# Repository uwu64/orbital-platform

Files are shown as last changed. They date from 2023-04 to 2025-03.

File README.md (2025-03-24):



# Orbital Platform

Integrated flight systems board with flight controller, avionics & instrumentation, radio, science, and development support for UC Davis Space and Satellite Systems REALOP-1 mission.

It's nearly all you need to fly a simple satellite and perform interesting experiments and observations 

## Documentation:

For an overview of the project, some FAQs, and links to some other documentation, see the [Cattleworks Compendium](https://docs.google.com/document/d/1Hi_DiSkjC-WS4wI39fk3itqsipQI5O-aAOiK9zkmOj8/edit#)

Pinout and usage information of Revision 3 can be found in the [OPR3 Reference Manual](https://docs.google.com/document/d/1Jm04JslQRQYXkw6q29EbMsp4aHQEIRqEN40WjQPSD0c/edit?usp=sharing)

Other useful documents include
- [STM32L47xxx reference manual](https://www.st.com/resource/en/reference_manual/rm0351-stm32l47xxx-stm32l48xxx-stm32l49xxx-and-stm32l4axxx-advanced-armbased-32bit-mcus-stmicroelectronics.pdf)
- [STM32L476xx datasheet](https://www.st.com/resource/en/datasheet/stm32l476zg.pdf)

Find IntelliSat developed by the flight software team at [the IntelliSat repository](https://github.com/Space-and-Satellite-Systems-UC-Davis/IntelliSat), including [detailed documentation about widgets and connections](https://github.com/Space-and-Satellite-Systems-UC-Davis/IntelliSat/blob/main/Manuals/OrbitalPlatform_Hardware/OP_Hardware.md). 

### Toolchain
Besides Flight Software's IntelliSat, I recommend that you try my [minimum development template](https://github.com/uwu64/cg3-stm32l476) that includes the exact bare minimum to compile and deploy firmware to Orbital Platform. The only dependencies are GCC for arm, pyocd, and make. 



## Revision 3

Revision 3 is in the validation stage, with many changes and additions. 

Some themes and guidelines for Revision 3: 
- Keep software compatibility with R2. Remap a minimal number of pins and don't change existing peripherals. 
- Further improve manufacturability.
- Include radio system (Orbital Imager will be deprecated)
  - Relatedly, we need a new camera interface port. Likely UART or SPI
- Possibly introduce additional features 
  - More connectors: Coils, panel temperature sensors, etc. 
  - More sensors: High precision temperature sensor, and digitizer for additional thermistors or sensors 
- Mechanical adjustments to meet any changes to structures, and possible compatibility with High Altitude Balloon project 
- Direct battery voltage measurement 
- Current sensor and power switches for ADCS science and experiment payloads
- Another redundant set of avionics (IMU and mag) for good vibes. IMU does not need to be at dead center of board anymore
- Multiple connectors and associated pins for features like HDD-ESC and sun sensors
- Heart beat LED on PE2 

Errata: a few things need to be fixed 
- Re-pour copper planes to fix two shorted vias
- Correct the direction of the PMOS high side switch for the pyro/antenna deployment heater
- MCU ADC Vref needs to be tied to either 3.3 V or external reference 

Related electrical team design tasks: 
- Three channel constant current driver for magnetorquer
- Hard disk drive motor driver

Inter-board connector list for Rev 3
| Mnemonic | Multiplicity | Connector type | Purpose |
| --- | --- | --- | --- |
| esc | 1 | Picoblade 4 pin | HDD driver speed command and feedback |
| coil | 1 (3 axis) | Picoblade 4 pin | Magnetorquer driver control signal and I V feedback |
| sol | 4-6 | Picoblade 8 pin | Sun sensor photodiodes and outer panel thermistors |
| mbat | 1 | Picoblade 8 pin | Satellite main battery |
| cam | 1 | Picoblade 8 pin | Imaging system data connection | 
| pyro | 1 | Picoblade 4 pin | Antenna melt-wire deployer |
| pv | 4 | Picoblade 8 pin | Photovoltaic cell (solar panel) power input from each panel |
| inst | 1-2 | Picoblade 8 pin | Auxiliary instrumentation bus (I2C) for remote ADCs |
| service | 1 | JST GH | Ground diagnostic and firmware service port (SWD, UART) | 
| topoff | 1 | N/A | Ground battery top-off charging port |
| rbf | 1 | N/A | Remove before flight safety interlock |
| aux | 1-4 | Picoblade 8 pin | Auxillary UART/I2C/SPI ports | 
| usb | 1 | USB Type-C | Ground use USB port |
| trx | 1 | MMCX | Antenna coaxial RF connection to radio system |

(Service and Topoff ports could be combined into "umbilical" port?)

Featured chips: (Many ~~chips~~ are removed for Revision 2. See below.)
 - STM32L476ZGT3 (microcontroller)
 - ASM330LHH (inertial sensor)
 - QMC5883L (magnetometer)
 - ~~ADF7021 (radio front end)~~ 
 - ~~TQP7M9102 (power amplifier)~~ 
 - ~~SKY13453 (rf switch)~~
 - ~~MAX2208 (rf power detector)~~ 
 - W25Q128JVSIQ (flash memory) 
 - MB85RS256B (ferroelectric memory)
 - ~~TMP235 (analog temperature sensor)~~ 

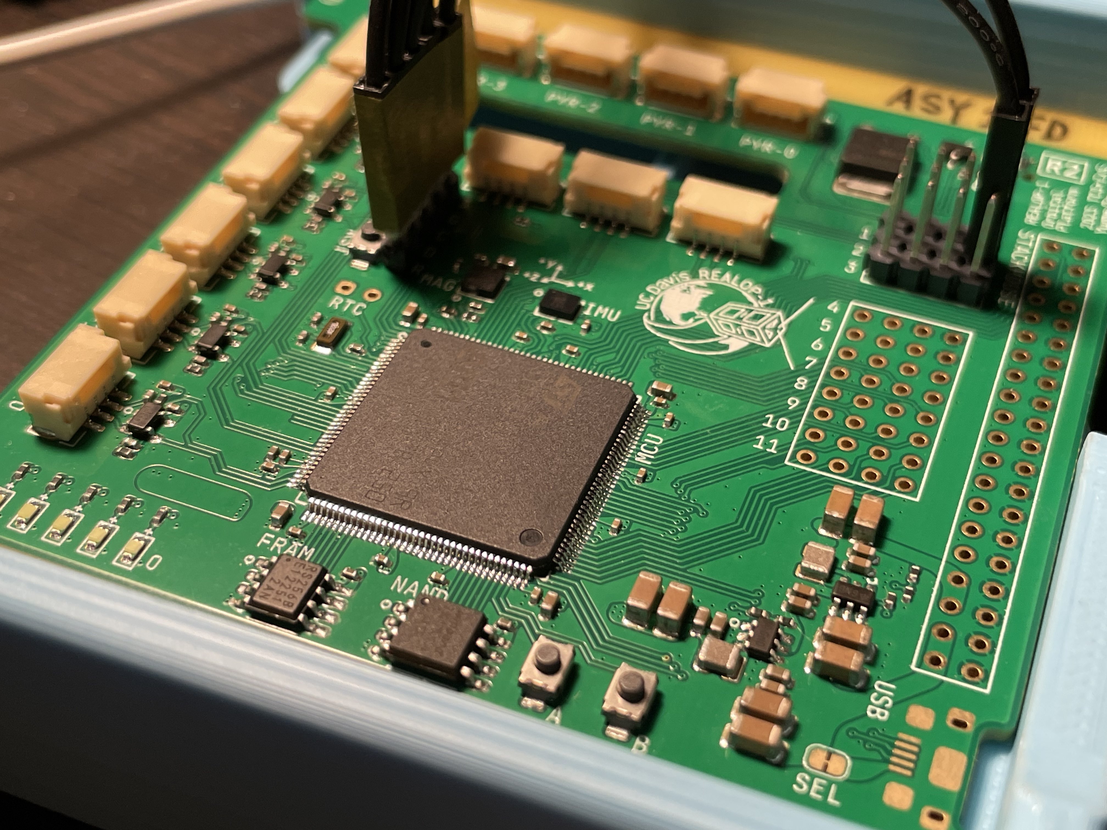
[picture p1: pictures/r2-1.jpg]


## Revision 2

Revision 2 hardware of Orbital Platform is in the verification stage. So far, so good!

### Changes 
- Removed radio system: communication function delegated to the new [Orbital Imager](https://github.com/REALOP-ELEC/Orbital_Imager_LRes) 
- Revised layout to improve routing, manufactuability, and reliabiltiy
- Inertial sensor (ASM330LHH) is now connected via SPI for reliability
- Magnetometer (QMC5883L) on its own I2C bus for reliability
- Addition of JST-GH connectors for
  - 6x Solar panels (photodiode + thermistor)
  - 4x Solar panels (pyramid design) 
  - ESC control via PWM
  - ESC control via UART
  - Expansion UART
- Addition of pyrotechnic channel to drive antenna deployment meltwire
- Less LEDs (still a usable amount)
- Fixed EXTI pins: no overlapping signals
- Fixed USB FS implementation 
- Design for manufacturability: reduced cost and BOM lines

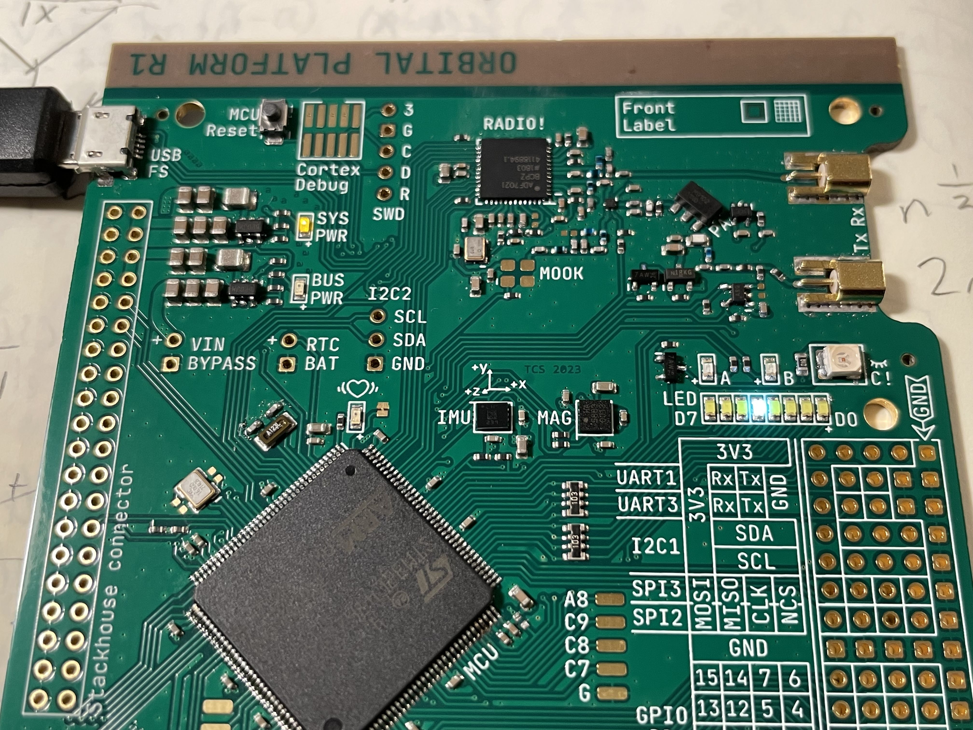
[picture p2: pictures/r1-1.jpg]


## Revision 1

Revision 1 was the initial prototype that we used to validate whether our choice of components are suited for the application. 

# Getting started

Orbital Platform should be delivered to you with a test program flashed, where it blinks the indicator LEDs in a demo pattern. 

To program and debug the MCU, attach a SWD-compatible debugger like ST-LINK, JLINK, or DAPLINK, to the SWD connector near the MCU. 
| Label | Signal |
| --- | --- |
| 3 | 3.3 V  |
| G | Ground |
| C | SWCLK  |
| D | SWDIO  |
| R | NRST |

The reset button is next to the SWD header, labelled RST. 

Use your toolchain of choice to target the `stm32l476zgt` MCU. 

## Using the gcc-arm-none-eabi toolchain and pyocd with DAPLINK debugger
I personally prefer to use a very minimal environment for prototyping firmware. See the [template project here](https://github.com/uwu64/cg3-stm32l476)

## Using the Keil MDK (μVision) IDE with DAPLINK debugger

One toolchain that works with developing software for Orbital Platform uses the Keil MDK IDE and DAPLINK debugger dongle, on Windows. 
- Start by downloading and installing a free version of Keil MDK-ARM (μVision). You should be able to download it after filling out some info on [the download page](https://www.keil.com/demo/eval/arm.htm)
  - The free version now seems to be called "MDK-Community" and appears to be a non-commercial but fully featured version of the normal IDE. It used to be that the demo/eval/free version had a very restricted code size. Hope this is no longer the case.
- Also download and install STM32CubeMX which is ST's initialization code generator and graphical config editor. Scroll down on [this page](https://www.st.com/en/development-tools/stm32cubemx.html) to Get Software. You might need to fill in some info for this as well. 
- Launch the IDE.
- Find the "Pack Installer" in the top toolbar. It looks like a green diamond shape with four dots inside.
- Use the Pack Installer to install relevant CMSIS device support packs for `STM32L4 Series`
- Close Pack Installer. From the top toolbar, use the menu `Project` -> `New μVision Project` to start a new project.
- When given the option to select target device, choose `STM32L476ZGTx`
- When given the option to manage run time environment, enable `CMSIS -> CORE`, `Device -> Startup`, `Device -> STM32Cube HAL`. There may be dependancies highlighted in yellow, enable those too.
  - Also enable `Device -> STM32Cube Framework (API) -> STM32CubeMX`. If it requires you to press the button to launch CubeMX, do it. Try to proceed with default settings in CubeMX because we don't intend to use any generated code.
  - Don't enable anything else unless you want to use full HAL or other middleware.
- After creating a new project, open `Options for Target` in the top toolbar. Then go to the `Debug` tab and choose Use `CMSIS-DAP debugger`. No additional configuration should be needed.
  - Or choose whatever debugger you use, like ST-Link or J-Link.
- In the left side `Project` panel, right click `Source Group 1` and select `Add new Item to Group`
  - Choose `C File (.c)` and name it `main.c`
  - You need to `#include <stm32l476xx.h>` to import register definitions.
  - Paste some code from this repository or write some blinky program.
  - Alternatively, you can git clone or zip download this repository and directly open the Keil project files. Everything should be configured for DAPLINK targeting Orbital Platform.
- Connect Orbital Platform to DAPLINK via the SWD port. Plug DAPLINK to your computer.
  - The DAPLINK should light up, if it doesn't, unplug it from your computer immediately and check your wiring. There may be a short circuit.
- Click `Build` on the top toolbar, then `Download`. Your code should now be compiled and flashed to Orbital Platform. Click `Debug` to launch the debugger, or signal a hardware reset to begin execution.

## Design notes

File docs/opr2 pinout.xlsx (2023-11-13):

Orbital Platform R2 |  | Pin definitions | Tim S. 2023 10 25 19 16
Pin | AF/Mode | Signal name | Definition
Pyro channel (melt-wire connector on bottom side)
PA0 | GPIO OUT | pyro-gate | High side switch control signal. Active high.
PA3 | ADC IN | pyro-isen | Current monitor for melt-wire. Voltage is proportional to current.
Solar panel sensor connectors (SOL-x)
PA1 | ADC IN | ntc-0 | Thermister divider output.
PA2 | ADC IN | pd-0 | Photodiode transimpedance amplifier output.
PC2 | ADC IN | ntc-1 | As above
PC3 | ADC IN | pd-1 | As above
PF9 | ADC IN | ntc-2 | As above
PF10 | ADC IN | pd-2 | As above
PF7 | ADC IN | ntc-3 | As above
PF8 | ADC IN | pd-3 | As above
PF5 | ADC IN | ntc-4 | As above
PF6 | ADC IN | pd-4 | As above
PF4 | ADC IN | ntc-5 | As above
PF3 | ADC IN | pd-5 | As above
Sun sensor pyramid connectors (PYR-x)
PF0 | AF I2C | sun-sda | I2C bus for sun sensor pyramids
PF1 | AF I2C | sun-scl | I2C bus for sun sensor pyramids
ESC controller (ESC-x)
PA15 | AF TMR CHx | esc-pwm | PWM output for ESC
PB6 | AF UART | esc-uart-tx | UART for custom ESC
PB7 | AF UART | esc-uart-rx | As above
Science expansion port (SCI-A)
PC0 | AF UART | sci-uart-rx | UART for future use
PC1 | AF UART | sci-uart-tx | As above
IMU on SPI3
PB3 | AF SPI | imu-sck
PB4 | AF SPI | imu-miso
PB5 | AF SPI | imu-mosi
PG15 | GPIO OUT | imu-ncs
PG12 | GPIO IN PU | imu-int1
PG13 | GPIO IN PU | imu-int2
MAG on I2C1
PB8 | AF I2C | mag-scl
PB9 | AF I2C | mag-sda
PE0 | EXTI0 | mag-drdy
FRAM on SPI1
PA4 |  | fram-ncs
PA5 |  | fram-sck
PA6 |  | fram-miso
PA7 |  | fram-mosi
PC4 |  | fram-nwp
PC5 |  | fram-nhold
NAND on QSPI
PE10 |  | nand-sck
PE11 |  | nand-ncs
PE12 |  | nand-d0
PE13 |  | nand-d1
PE14 |  | nand-d2
PE15 |  | nand-d3
Stackhouse power regulator
PB12 | GPIO OUT | vout-en | Enable signal for regulator
PB13 |  | vout-pg | Power good signal from regulator. Active low when voltage is in range
Indicator LEDs
PE2 | GPIO OUT | led4
PE3 | GPIO OUT | led3
PE4 | GPIO OUT | led2
PE5 | GPIO OUT | led1
PE6 | GPIO OUT | led0
User buttons
PB10 | GPIO IN PU | btn-a
PB11 | GPIO IN PU | btn-b
Stackhouse connector
PD15 |  | stack-bus-good
PG2 |  | stack-pa-en
PG3 |  | stack-pa-temp
PG4 |  | stack-pa-det
PG5 |  | stack-rfd-temp
PG8 |  | stack-i2c-sda
PG7 |  | stack-i2c-scl
PC10 |  | instbus-int0
PC11 |  | radiobus-int0
PD0 |  | radio-spi-cs
PD3 |  | radio-spi-rofi
PD4 |  | radio-spi-rifo
PD1 |  | radio-spi-clk
Debug GPIOs (labeled from left to right, 1 to 4)
1-1 | GND
1-2 | esc-pwm
1-3 | esc-uart-rx
1-4 | esc-uart-tx
2-1 | mag-scl
2-2 | imu-mosi
2-3 | imu-ncs
2-4 | sci-uart-rx
3-1 | mag-sda
3-2 | imu-miso
3-3 | imu-sck
3-4 | sci-uart-tx
4-1 | 3V3
4-2 | 3V3
4-3 | GND
4-4 | GND
5-1 | PF15
5-2 | PF14
5-3 | PF13
5-4 | GND
6-1
6-2
6-3
6-4

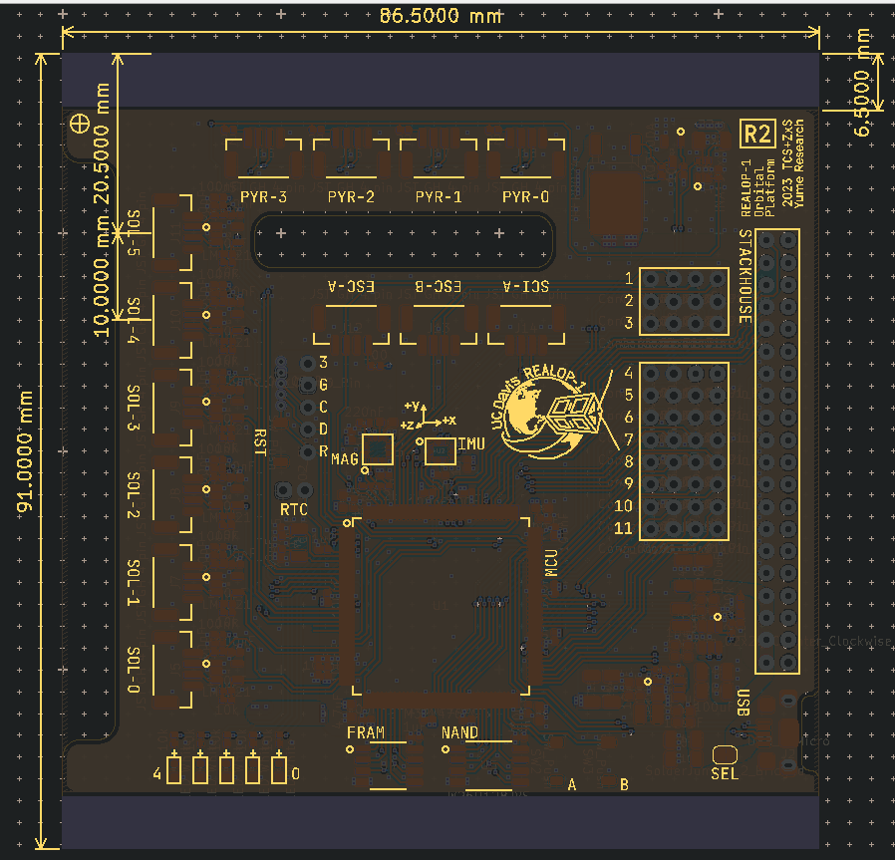
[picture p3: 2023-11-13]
docs/r2-mech.png

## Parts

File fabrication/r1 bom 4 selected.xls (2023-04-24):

Comment | Designator | Footprint | JLCPCB Part #
1n | C48,C50,C59,C70,C73 | C0402 | C113780
3.3k | R32 | C0402 | C25890
1.5k | R6 | C0402 | C25867
22u | C1,C2,C3,C4,C5,C42,C43,C44,C45,C46 | C0805 | C45783
LEDRed | D11 | LED0603v2 | C84263
220 | R42 | C0402 | C25117
4.7k | R7,R8,R13,R14,R15,R16,R26,R28,R33,R34 | C0402 | C25900
10k | R9,R10,R11,R12,R17,R20,R21,R22,R25,R36,R37,R38,R39 | C0402 | C25744
32.768k | X1 | XO3215-2P | C32346
24M | X2 | XO3225 | C13738
100k | R1,R18 | C0402 | C25741
LEDWhite | D1,D2,D3,D4,D5,D6,D7,D8 | LED0603v2 | C84265
LEDBlue | D12,D15 | LED0603v2 | C84266
10 | R24 | C0402 | C25077
10p | C52 | C0402 | C32949
2.7p | C74,C75 | C0402 | C1561
3.3p | C56,C71,C72 | C0402 | C1565
10u | C26,C60,C61,C62,C63,C64,C65,C68,C69,C76 | C0603 | C19702
22p | C47,C51 | C0402 | C1555
1u | C6,C12,C13,C14,C15,C16,C17,C18,C23,C24,C25,C27,C29,C30,C31,C32,C33,C34,C35,C36,C37,C38,C39,C40,C41,C49,C53,C55,C58,C66,C77,C80 | C0402 | C52923
220n | C67 | C0402 | C16772
100p | C79,C81 | C0402 | C1546
15p | C78 | C0402 | C1548
10k | R4,R5 | R0603x4 | C29718
1k | R3,R29,R30,R31,R44 | C0402 | C11702
6.8n | C20 | C0402 | C1542
FB0603 | FB1 | C0603 | C13415
LEDYellow | D9,D13,D14 | LED0603v2 | C72038
100n | C19,C21,C28,C54,C57 | C0402 | C1525
22n | C22 | C0402 | C1532
2.2n | C9 | C0402 | C1531
100 | R35 | C0603 | C22775
LEDGreen | D10 | LED0603v2 | C84267
0 | R40,R41 | C0402 | C17168
39n | L7,L8 | C0402 | C269823
ICQMC5883L | U9 | LGA16-5 | C976032
56n | L6,L9,L10 | C0402 | C167484
22k | R2,R19 | C0402 | C25768
QSi2301 | Q2 | SOT23-3 | C10487
ICSKY13453 | U8 | QFN6 | C150878
10n | L5,L12 | C0402 | C90642

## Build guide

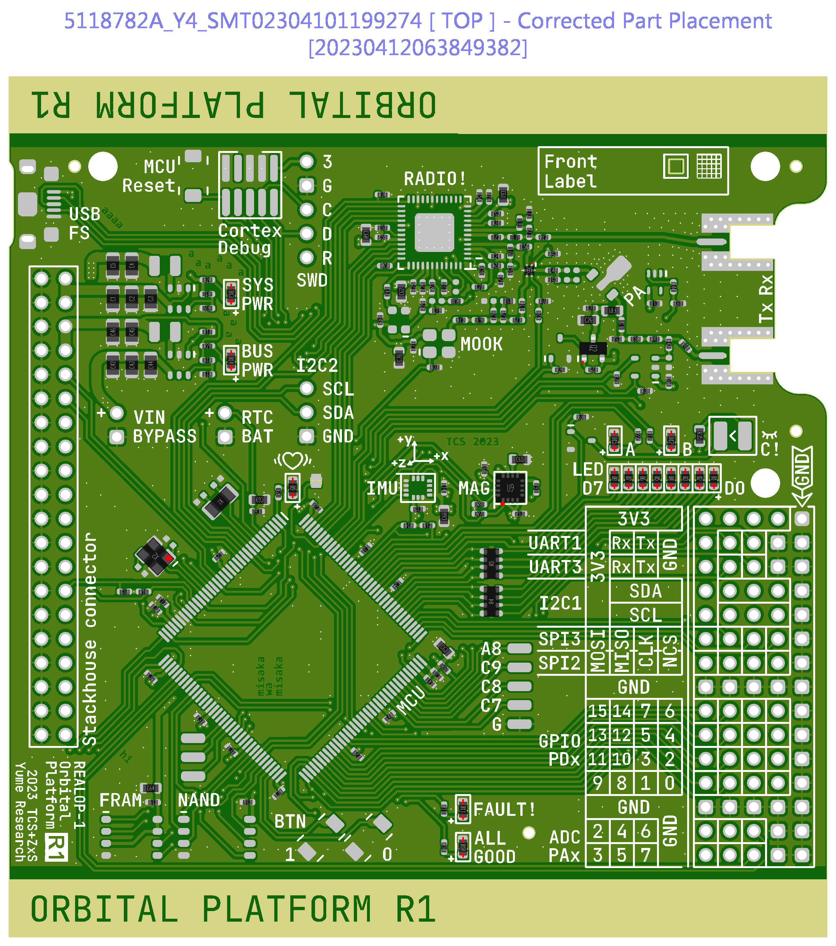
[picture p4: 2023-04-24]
fabrication/r1-img.png

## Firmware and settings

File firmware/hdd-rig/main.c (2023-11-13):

// opr2-quickstart1 
// Quick start for Orbital Platform R2 
// TCS 202310. Yume Research & Friends. 
// The above attribution must be included regardless of license. 
// This is not permissively licensed software. 

//  

#include <stm32l476xx.h>
#include <math.h> // for sqrt 
typedef enum { false, true } bool;

#include <string.h>
/* reverse:  reverse string s in place */
static void reverse(char s[]) {
	int i, j;
	char c;

	for (i = 0, j = strlen(s)-1; i<j; i++, j--) {
		c = s[i];
		s[i] = s[j];
		s[j] = c;
	}
}  

 /* itoa:  convert n to characters in s */
static void itoa(int n, char s[]) {
	int i, sign;
	if ((sign = n) < 0)  /* record sign */
		n = -n;          /* make n positive */
	i = 0;
	do {       /* generate digits in reverse order */
		s[i++] = n % 10 + '0';   /* get next digit */
	} while ((n /= 10) > 0);     /* delete it */
	if (sign < 0)
		s[i++] = '-';
	s[i] = '\0';
	reverse(s);
}  

unsigned int abs16(int16_t a) {
	if (a < 0) {
		return (a * -1);
	} else {
		return a;
	}
}

void nop(int nop_loops) {
	for (int i = 0; i < nop_loops; i++) {__NOP();}
}

void nop_ms(int ms) {
	nop(80 * 250 * ms); // assume 80 MHz 
}

int core_MHz = 0; // please update when configuring pll. not really used rn 
void init_clocks() {
	// read chip identification information. only useful when watching memory through debugger 
	volatile int id_w_x = (*(uint32_t*)(UID_BASE) & 0xFFFF0000) >> 16;
	volatile int id_w_y = *(uint32_t*)(UID_BASE) & 0xFFFF;
	volatile int id_w_n = *(uint32_t*)(UID_BASE+0x4) & 0xFF;
	volatile int id_lot_l = *(uint32_t*)(UID_BASE+0x4) & 0xFFFFFF00;
	volatile int id_lot_h = *(uint32_t*)(UID_BASE+0x8);
	volatile char id_lot[7] = {
		(id_lot_l >> 8) & 0xFF,
		(id_lot_l >> 16) & 0xFF,
		(id_lot_l >> 24) & 0xFF,
		(id_lot_h) & 0xFF,
		(id_lot_h >> 8) & 0xFF,
		(id_lot_h >> 16) & 0xFF,
		(id_lot_h >> 24) & 0xFF
	};
	RCC->AHB2ENR = 0x000530FF; // enable clock to all gpio banks, usb otg, adc, crypto 
	RCC->AHB3ENR = 0x00000100; // enable clock to QSPI 
	RCC->APB1ENR1 = 
		1 << 28 // enable power control 
		| 1 << 22 // enable i2c2 
		| 1 << 15 // enable spi3 
		| 1 << 14 // enable spi2 
		| 1 << 10; // enable rtc apb 
	RCC->APB1ENR2 = 
		1 << 0; // enable lpuart1 
	RCC->APB2ENR = 1; // enable syscfg 
	FLASH->ACR = 0x600 | 4 | 1<<8; // flash access latency to four wait states, prefetch enable lol 
	//FLASH->ACR = 0x604; // OVERCLOCK! for testing only 
	RCC->CR |= 1 << 8; // enable HSI 
	RCC->PLLCFGR = 
		0x0 << 25 // PLLR = 2 
		| 1 << 24 // PLLREN = 1 
		| 0x0 << 21 // PLLQ = 2 
		| 1 << 20 // PLLQEN (PLL48M1CLK) output enabled 
		| 0x0 << 17 // PLLP default 
		| 0 << 16 // PLLSAI3 not enabled  
		 | 10 << 8 // PLLN = 10 
	//	| 20 << 8 // OVERCLOCK! for testing only 
		| 0 << 4 // PLLM = 1 
		| 0x2; // HSI16 as input clock to PLLs 
	RCC->PLLSAI1CFGR = 
		0x1 << 25 // PLLSAI1R = 4 
		| 1 << 24 // PLLSAI1REN = PLLADC1CLK enable 
		| 0x1 << 21 // PLLSAI1Q = 4
		| 1 << 20 // PLLSAI1QEN = PLL48M2CLK enable
		| 0x0 << 17 // PLLSAI1P = default 
		| 0 << 16 // PLLSAI1PEN = 0
		| 12 << 8; // PLLSAI1N = 12 
	RCC->CR |= (1 << 24) | (1 << 26); // enable PLL and PLLSAI1 
	while (!(RCC->CR & (1 << 25))); // wait for PLL lock 
	while (!(RCC->CR & (1 << 27))); // wait for PLLSAI1 lock 
	RCC->CFGR = 0x3; // system clock to PLL 
	core_MHz = 80;
}

void gpio_high(GPIO_TypeDef * port, int pin) {
	port->BSRR = 1 << pin;
}

void gpio_low(GPIO_TypeDef * port, int pin) {
	port->BSRR = 1 << (pin+16);
}

void gpio_set(GPIO_TypeDef * port, int pin, int value) {
	if (value) {
		gpio_high(port, pin);
	} else {
		gpio_low(port, pin);
	}
}

int gpio_read(GPIO_TypeDef * port, int pin) {
	if (port->IDR & (1 << pin)) {
		return 1;
	} else {
		return 0;
	}
}


#define GPIO_DIGITAL_IN		0 
#define GPIO_DIGITAL_OUT	1 
#define GPIO_AF 			2 
#define GPIO_ANALOG_IN 		3 
#define GPIO_PUSH_PULL 		0 
#define GPIO_OPEN_DRAIN		1 
#define GPIO_LOW_SPEED		0 
#define GPIO_MED_SPEED		1 
#define GPIO_HI_SPEED		2 
#define GPIO_VERY_HI_SPEED	3 
#define GPIO_NO_PULL		0 
#define GPIO_PULL_UP		1 
#define GPIO_PULL_DOWN		2 

void gpio_mode(GPIO_TypeDef * port, int pin, int mode, int open_drain, int speed, int pull) {
	port->MODER = (port->MODER & ~(0x3 << (pin*2))) | ((mode & 0x3) << (pin*2)); // 0 digital in with schmitt trigger, 1 output, 2 AF, 3 analog mode 
	port->OTYPER = (port->OTYPER & ~(0x1 << pin)) | ((open_drain & 0x1) << pin); // 0 is normal push pull, 1 is open drain 
	port->OSPEEDR = (port->OSPEEDR & ~(0x3 << (pin*2))) | ((speed & 0x3) << (pin*2)); // 0x3 is very high speed, 0x0 is normal low speed 
	port->PUPDR = (port->PUPDR & ~(0x3 << (pin*2))) | ((pull & 0x3) << (pin*2)); // 0 no pupd, 1 pu, 2 pd, 3 reserved 
}

void gpio_af(GPIO_TypeDef * port, uint8_t pin, uint8_t afn) {
	port->MODER = (port->MODER & ~(0x3 << (pin*2))) | ((0x2) << (pin*2)); 
	if (pin > 7) {
		port->AFR[1] = (port->AFR[1] & ~(0xF << ((pin-8)*4))) | ((afn & 0xF) << ((pin-8)*4)); 
	} else {
		port->AFR[0] = (port->AFR[0] & ~(0xF << (pin*4))) | ((afn & 0xF) << (pin*4)); 
	}
	gpio_low(port, pin); 
}

void init_gpio() {
	PWR->CR2 |= 1 << 9; // enable VDDIO2 supply for GPIOG 
	
	// wait until each GPIO is clocked and ready: 
	// (there is a delay before perph is enabled after RCC to synchronize internal bus stuff)
	while (GPIOA->OTYPER == 0xFFFFFFFF); 
	while (GPIOB->OTYPER == 0xFFFFFFFF); 
	while (GPIOC->OTYPER == 0xFFFFFFFF); 
	while (GPIOD->OTYPER == 0xFFFFFFFF); 
	while (GPIOE->OTYPER == 0xFFFFFFFF); 
	while (GPIOF->OTYPER == 0xFFFFFFFF); 
	while (GPIOG->OTYPER == 0xFFFFFFFF); 
	
	gpio_mode(GPIOB, 10, 0, 0, 0, 1); // BTNA - input with schmitt trigger, not open drain, low speed, pull up 
	gpio_mode(GPIOB, 11, 0, 0, 0, 1); // BTNB 
	
	gpio_mode(GPIOE, 6, 1, 0, 0, 0); // LED0 - output, not OD, low speed, no pull 
	gpio_mode(GPIOE, 5, 1, 0, 0, 0); // LED1 
	gpio_mode(GPIOE, 4, 1, 0, 0, 0); // LED2 
	gpio_mode(GPIOE, 3, 1, 0, 0, 0); // LED3 
	gpio_mode(GPIOE, 2, 1, 0, 0, 0); // LED4 
}

unsigned int systick_time = 0; 
void SysTick_Handler() {
	systick_time++;
}

void delay_ms(unsigned int ms) {
	if (!ms) return; 
	unsigned int target = systick_time + ms; 
	while (target < systick_time) {__NOP();}; // in case overflow and wrapping 
	while (target > systick_time) {__NOP();}; 
}

void init_nvic() {
	__disable_irq();
	SysTick->LOAD = core_MHz/8*1000; // configure for 1 ms period, use AHB/8 
	SysTick->CTRL = 0x3; // use AHB/8 as input clock, enable interrupts and counter 
	NVIC_EnableIRQ(SysTick_IRQn);
	__enable_irq();
}

// i just implemented against lpuart. brr calculation for normal u(s)art might differ 
void init_lpuart(USART_TypeDef * uart,
	GPIO_TypeDef * tx_port, int tx_pin, int tx_afn, 
	GPIO_TypeDef * rx_port, int rx_pin, int rx_afn) {
	// assume peripheral is already enabled in RCC 
	
	gpio_af(tx_port, tx_pin, tx_afn);
	gpio_af(rx_port, rx_pin, rx_afn);
	
	uart->BRR = 177778; // approx 115200 with 80 MHz: (256·80MHz)/x = 115200Hz
	uart->CR3 = 0; // not really using anything here 
	uart->CR2 = 0 << 12; // 1 stop bit.. the defaults are fine here again 
	uart->CR1 = 
		(0 << 28)|(0 << 12) // 1 start bits, 8 data bits, n stop bits 
		| 1 << 3 // transmitter enable. this generates a preamble immediately 
		| 1 << 2 // receiver enable lol 
		| 1 << 0; // enable uart  
}

void uart_tx_char(USART_TypeDef * uart, uint8_t data) {
	while (!(uart->ISR & 1<<7)) {__NOP();}; // while not TXE 
	uart->TDR = data; 
}

void uart_tx_long(USART_TypeDef * uart, int len, uint8_t * data) {
	for (int i = 0; i < len; i++) {
		while (!(uart->ISR & 1<<7)) {__NOP();}; // while not TXE 
		uart->TDR = data[i]; 
	}
	while (!(uart->ISR & 1<<6)) {__NOP();}; // while not TC 
}

//UNUSED! (wanted to make sure we can hit 115200 baud for spin demo) 
void init_softuart(GPIO_TypeDef * tx_port, int tx_pin, GPIO_TypeDef * rx_port, int rx_pin) {
	gpio_set(tx_port, tx_pin, 1); 
	gpio_mode(tx_port, tx_pin, GPIO_DIGITAL_OUT, GPIO_PUSH_PULL, GPIO_HI_SPEED, GPIO_NO_PULL);
	gpio_mode(rx_port, rx_pin, GPIO_DIGITAL_IN, 0, GPIO_HI_SPEED, GPIO_PULL_DOWN);
}

//UNUSED:
void softuart_tx_char(GPIO_TypeDef * tx_port, int tx_pin, GPIO_TypeDef * rx_port, int rx_pin, int data) {
	
}

void init_spi_master(SPI_TypeDef * spi, 
	GPIO_TypeDef * mosi_port, int mosi_pin, int mosi_afn, 
	GPIO_TypeDef * miso_port, int miso_pin, int miso_afn, 
	GPIO_TypeDef * sck_port, int sck_pin, int sck_afn, 
	GPIO_TypeDef * ncs_port, int ncs_pin) {
	// assume peripheral is already enabled in RCC 
	
	gpio_af(mosi_port, mosi_pin, mosi_afn);
	gpio_af(miso_port, miso_pin, miso_afn);
	gpio_af(sck_port, sck_pin, sck_afn);
	gpio_set(ncs_port, ncs_pin, 1); 
	gpio_mode(ncs_port, ncs_pin, 1, 0, 0, 0);
	
	spi->CR2 = 0x0700 // default value on reset.. ok this whole thing is redundant, default values are fine honestly 
		| 1 << 12 // FRXTH: RXNE event generated if FIFO lvl >= 1/4 (for 8 bit)
		| 0x7 << 8 // data size: 8 bits 
		| 0 << 7 // TXE interrupt enable = disable 
		| 0 << 6 // RXNE i. disabled 
		| 0 << 5 // ERR i. disabled 
		| 0 << 4 // spi motorola mode 
		| 0 << 3 // no nss pulse between consecutive frames 
		| 0 << 2 // CS output disabled 
		| 0 << 1 // tx dma disabled 
		| 0 << 0; // rx dma disabled 
	spi->CR1 = 0 
		| 1 << 9 // software slave management enabled 
		| 1 << 8 // internal slave selected 
		| 0x7 << 2 // baud rate control: divide fpclk by 2^x 
		| 1 << 2 // master mode 
		| 0 << 1 // CPOL = 0: SCK to 0 when idle 
		| 0 << 0 // CPHA = 0: data capture edge is first clock transition 
		| 1 << 6; // enable SPI 
}

int spi_block_while_busy(SPI_TypeDef * spi) {
	while (spi->SR & (1<<7)) {__NOP();} // wait while busy
}

void spi_tx8(SPI_TypeDef * spi, int data) {
	while (!(spi->SR & (1<<1))) {__NOP();} // wait while tx buffer is not empty
	*(volatile uint8_t*)&spi->DR = data & 0xFF;
	while (!(spi->SR & (1<<1))) {__NOP();} // wait while tx buffer is not empty before checking bsy
//	while (spi->SR & (1<<7)) {__NOP();} // wait while busy 
//	return spi->DR; // if want to clear OVR flag, read DR then read SR. both fifo should be balanced here so im not doing that
}

uint16_t spi_rx8(SPI_TypeDef * spi) {
	return spi->DR; 
}

void spi_tx8x2(SPI_TypeDef * spi, int data1, int data2) {
	while (!(spi->SR & (1<<1))) {__NOP();} // wait while tx buffer is not empty
	*(volatile uint8_t*)&spi->DR = data1 & 0xFF;
	while (!(spi->SR & (1<<1))) {__NOP();} // wait while tx buffer is not empty before checking bsy
//	while (spi->SR & (1<<7)) {__NOP();} // wait while busy 
//	int hi = spi->DR; // dummy read 
	*(volatile uint8_t*)&spi->DR = data2 & 0xFF;
	while (!(spi->SR & (1<<1))) {__NOP();} // wait while tx buffer is not empty before checking bsy
//	while (spi->SR & (1<<7)) {__NOP();} // wait while busy 
//	hi = spi->DR;
//	return spi->DR; 
}

void spi_tx8_long(SPI_TypeDef * spi, int len, int * txdata) {
	for (int i = 0; i < len; i++) {
		while (!(spi->SR & (1<<1))) {__NOP();} // wait while tx buffer is not empty
		*(volatile uint8_t*)&spi->DR = txdata[i] & 0xFF;
	}
	while (!(spi->SR & (1<<1))) {__NOP();} // wait while tx buffer is not empty before checking bsy
//	while (spi->SR & (1<<7)) {__NOP();} // wait while busy 
	int temp = spi->DR; // clearing OVR flag with dummy DR and SR read 
	temp = spi->SR; 
}

void spi_txrx8_long(SPI_TypeDef * spi, int len, int * txdata, int * rxdata) {
	for (int i = 0; i < len; i++) {
		while (spi->SR & (1<<7)) {__NOP();} // wait while busy 
		*(volatile uint8_t*)&spi->DR = txdata[i] & 0xFF;
		while (!(spi->SR & (1<<0))) {__NOP();} // wait while rx buf is empty 
		rxdata[i] = spi->DR; 
	}
} 

void softi2c_line_mode(GPIO_TypeDef * port, int pin, bool deassert_line) {
	if (deassert_line) {
		port->MODER &= ~(0x3 << (pin*2)); 
	} else {
		port->MODER = (port->MODER & ~(0x3 << (pin*2))) | (1 << pin*2); 
	}
}

void init_softi2c(GPIO_TypeDef * scl_port, int scl_pin, GPIO_TypeDef * sda_port, int sda_pin) {
	scl_port->OTYPER = (scl_port->OTYPER & ~(1 << scl_pin)) | (0 << scl_pin); // push pull 
	sda_port->OTYPER = (sda_port->OTYPER & ~(1 << sda_pin)) | (0 << sda_pin); 
	scl_port->OSPEEDR = (scl_port->OSPEEDR & ~(0x3 << (scl_pin*2))) | (3 << scl_pin*2); // very high speed 
	sda_port->OSPEEDR = (sda_port->OSPEEDR & ~(0x3 << (sda_pin*2))) | (3 << sda_pin*2); 
	scl_port->BSRR = 1 << (scl_pin + 16); // drive low when asserted 
	sda_port->BSRR = 1 << (sda_pin + 16);
	softi2c_line_mode(scl_port, scl_pin, 1); 
	softi2c_line_mode(sda_port, sda_pin, 1); 
}

void softi2c_delay() {
	nop(30);
}

void softi2c_sig_start(GPIO_TypeDef * scl_port, int scl_pin, GPIO_TypeDef * sda_port, int sda_pin) {
	softi2c_line_mode(scl_port, scl_pin, 1);
	softi2c_line_mode(sda_port, sda_pin, 1);
	softi2c_delay(); softi2c_delay();
	softi2c_line_mode(sda_port, sda_pin, 0);
	softi2c_delay(); softi2c_delay();
	softi2c_line_mode(scl_port, scl_pin, 0);
	softi2c_delay(); 
}

void softi2c_sig_repeated_start(GPIO_TypeDef * scl_port, int scl_pin, GPIO_TypeDef * sda_port, int sda_pin) {
	softi2c_line_mode(scl_port, scl_pin, 0);
	softi2c_line_mode(sda_port, sda_pin, 1);
	softi2c_delay();
	softi2c_line_mode(scl_port, scl_pin, 1);
	softi2c_delay(); softi2c_delay();
	softi2c_line_mode(sda_port, sda_pin, 0);
	softi2c_delay(); softi2c_delay();
	softi2c_line_mode(scl_port, scl_pin, 0);
	softi2c_delay(); 
}

void softi2c_sig_stop(GPIO_TypeDef * scl_port, int scl_pin, GPIO_TypeDef * sda_port, int sda_pin) {
	softi2c_line_mode(scl_port, scl_pin, 0);
	softi2c_line_mode(sda_port, sda_pin, 0);
	softi2c_delay(); softi2c_delay();
	softi2c_line_mode(scl_port, scl_pin, 1);
	softi2c_delay(); softi2c_delay();
	softi2c_line_mode(sda_port, sda_pin, 1);
	softi2c_delay(); 
}

void softi2c_send8(GPIO_TypeDef * scl_port, int scl_pin, GPIO_TypeDef * sda_port, int sda_pin, int data8) {
	for (int i = 0; i < 8; i++) {
		softi2c_line_mode(scl_port, scl_pin, 0);
		softi2c_delay();
		softi2c_line_mode(sda_port, sda_pin, (data8 << i) & (1 << 7));
		softi2c_delay(); 
		softi2c_line_mode(scl_port, scl_pin, 1);
		softi2c_delay(); softi2c_delay();
	}
}

int softi2c_read8(GPIO_TypeDef * scl_port, int scl_pin, GPIO_TypeDef * sda_port, int sda_pin) {
	int data = 0; 
	softi2c_line_mode(sda_port, sda_pin, 1);
	for (int i = 0; i < 8; i++) {
		softi2c_line_mode(scl_port, scl_pin, 0);
		softi2c_delay();
		data |= gpio_read(sda_port, sda_pin) << (7-i);
		softi2c_delay(); 
		softi2c_line_mode(scl_port, scl_pin, 1);
		softi2c_delay(); softi2c_delay();
	}
	return data;
}

void softi2c_send_nack(GPIO_TypeDef * scl_port, int scl_pin, GPIO_TypeDef * sda_port, int sda_pin) {
	softi2c_line_mode(scl_port, scl_pin, 0);
	softi2c_delay();
	softi2c_line_mode(sda_port, sda_pin, 1);
	softi2c_delay(); 
	softi2c_line_mode(scl_port, scl_pin, 1);
	softi2c_delay(); 
}

int softi2c_read_nack(GPIO_TypeDef * scl_port, int scl_pin, GPIO_TypeDef * sda_port, int sda_pin) {
	softi2c_line_mode(scl_port, scl_pin, 0);
	softi2c_delay();
	softi2c_line_mode(sda_port, sda_pin, 1);
	softi2c_delay(); 
	softi2c_line_mode(scl_port, scl_pin, 1);
	softi2c_delay(); 
	int nack = gpio_read(sda_port, sda_pin);
	softi2c_delay();
	return nack; 
}

int softi2c_write_reg(GPIO_TypeDef * scl_port, int scl_pin, GPIO_TypeDef * sda_port, int sda_pin, int device_addr, int reg_addr, int data) {
	int nack = 0; 
	softi2c_sig_start(scl_port, scl_pin, sda_port, sda_pin);
	softi2c_send8(scl_port, scl_pin, sda_port, sda_pin, device_addr << 1 | 0);
	nack += softi2c_read_nack(scl_port, scl_pin, sda_port, sda_pin);
	softi2c_send8(scl_port, scl_pin, sda_port, sda_pin, reg_addr);
	nack += softi2c_read_nack(scl_port, scl_pin, sda_port, sda_pin);
	softi2c_send8(scl_port, scl_pin, sda_port, sda_pin, data);
	nack += softi2c_read_nack(scl_port, scl_pin, sda_port, sda_pin);
	softi2c_sig_stop(scl_port, scl_pin, sda_port, sda_pin);
	return nack; 
}

int softi2c_read_reg(GPIO_TypeDef * scl_port, int scl_pin, GPIO_TypeDef * sda_port, int sda_pin, int device_addr, int reg_addr) {
	int nack = 0; 
	softi2c_sig_start(scl_port, scl_pin, sda_port, sda_pin);
	softi2c_send8(scl_port, scl_pin, sda_port, sda_pin, device_addr << 1 | 0);
	nack += softi2c_read_nack(scl_port, scl_pin, sda_port, sda_pin);
	softi2c_send8(scl_port, scl_pin, sda_port, sda_pin, reg_addr);
	nack += softi2c_read_nack(scl_port, scl_pin, sda_port, sda_pin);
	softi2c_sig_repeated_start(scl_port, scl_pin, sda_port, sda_pin);
	softi2c_send8(scl_port, scl_pin, sda_port, sda_pin, device_addr << 1 | 1);
	nack += softi2c_read_nack(scl_port, scl_pin, sda_port, sda_pin);
	int data = softi2c_read8(scl_port, scl_pin, sda_port, sda_pin);
	softi2c_send_nack(scl_port, scl_pin, sda_port, sda_pin);
	softi2c_sig_stop(scl_port, scl_pin, sda_port, sda_pin);
	return data;
}
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
int main() {
	op2_core_init(); 
	
	gpio_set(GPIOE, 2, 1); 
	
	op2_sci_uart_init();
	op2_imu_init(IMU_ODR_3333_Hz, IMU_FS_2_g, IMU_ODR_3333_Hz, IMU_FS_1000_dps);
	op2_mag_init(MAG_ODR_200_Hz, MAG_FS_8_G, MAG_OVERSAMPLE_512);
	
	int state = 0;
	int btn_debounce = 0;
	
	gpio_set(GPIOE, 2, 0); 
	
	// output factory info 
	op2_printstr("orbital platform r2. mcu serial bytes: "); 
	op2_printuint32(*(uint32_t*)(UID_BASE));
	op2_printstr(", ");
	op2_printuint32(*(uint32_t*)(UID_BASE+0x4));
	op2_printstr(", ");
	op2_printuint32(*(uint32_t*)(UID_BASE+0x8));
	op2_printnewline();
	
	op2_imu_read_whoami();
	
	
	int btna_pressed_at_start = gpio_read(GPIOB, 10); 
	
	if (!btna_pressed_at_start) {gpio_set(GPIOE, 4, 1);}  // diagnostic mode if btna is pressed 
	else {
		gpio_set(GPIOE, 2, 1);
		gpio_set(GPIOE, 3, 1);
	}
	
	while (1) {
	//	if (btna_pressed_at_start) {gpio_af(GPIOA, 15, 1);} // output pwm if NOT in diagnostic mode 		
		gpio_af(GPIOA, 15, 1);
		RCC->APB1ENR1 |= 1<<0; 					// enable TIM2 
		delay_ms(1);
		TIM2->PSC = 81; 						// clock prescaler 
		TIM2->CCER = 1<<0;						// 
		TIM2->CCMR1 = (6 << 4) | (1 << 3);	// pwm mode, enable 
		TIM2->EGR = 1<<1; 						// give an event trigger to update shadow registers 
		TIM2->ARR = 10000;						// reload register 
		TIM2->CCR1 = 1000;					
		TIM2->CR1 = 
			(1 << 7) | 1; 						// enable auto reload preload and enable tim2 
		
		TIM2->CCR1 = 1500; // rc protocol: 1 ms is minimum, 2 ms is maximum 
		
		int th = 0 * 5; // esc throttle, plus or minus 100 
		TIM2->CCR1 = 1500 + th * 5;
		
	//	while(1);
		
		int targetms = 10; // delay before starting program 
		while (1) {
			if (systick_time >= targetms) {
				op2_printstr("cannot keep up! reduce output data rate.\r\n");
				op2_printstr("limited by uart baud rate.\r\n");
				while (1) __NOP();
			}
			
			if (systick_time> 5000) {
				th = (systick_time - 5000) / 100; 
				// 5 seconds: take 10 seconds to ramp to full throttle 
			} 
			if (systick_time > 15000) {
				th = 100; 
				// 15 seconds: full throttle 
			} 
			if (systick_time > 20000) {
				th = 0; 
				// 20 seconds: zero throttle 
			} 
			if (!btna_pressed_at_start) th = 0; 
			TIM2->CCR1 = 1500 + th * 5;
			
			while (systick_time < targetms) __NOP();
			
			op2_printuint32(systick_time);
			op2_printstr(",");
			op2_printint16(op2_imu_read_acel_x());
			op2_printstr(",");
			op2_printint16(op2_imu_read_acel_y());
			op2_printstr(",");
			op2_printint16(op2_imu_read_acel_z());
			op2_printstr(",");
			op2_printint16(op2_imu_read_gyro_x());
			op2_printstr(",");
			op2_printint16(op2_imu_read_gyro_y());
			op2_printstr(",");
			op2_printint16(op2_imu_read_gyro_z());
			op2_printstr(",");
			op2_printuint32(th);
			op2_printnewline();
			
			targetms += 5;
		}
	}
	
	
	
	
// 	while (1) {
// 		op2_print_sci("good evening! the current systick is: ");
// 		itoa(systick_time, textbuf);
// 		op2_print_sci(textbuf);
// 		op2_print_sci(" ms\r\n");
		
// 		op2_imu_read_whoami();
// 		op2_imu_read_acel_x();
// 		gpio_set(GPIOE, 6, 1); 
// //		delay_ms(500);
// 		gpio_set(GPIOE, 6, 0); 
// //		delay_ms(500);
// 	}

	while (0) { // blinky demo 
		gpio_set(GPIOE, 2, 1); 
		gpio_set(GPIOE, 3, 0); 
		delay_ms(60);
		gpio_set(GPIOE, 3, 1); 
		gpio_set(GPIOE, 2, 0); 
		delay_ms(60);
		gpio_set(GPIOE, 4, 1); 
		gpio_set(GPIOE, 3, 0); 
		delay_ms(60);
		gpio_set(GPIOE, 5, 1); 
		gpio_set(GPIOE, 4, 0); 
		delay_ms(60);
		gpio_set(GPIOE, 6, 1); 
		gpio_set(GPIOE, 5, 0); 
		delay_ms(60);
		gpio_set(GPIOE, 5, 1); 
		gpio_set(GPIOE, 6, 0); 
		delay_ms(60);
		gpio_set(GPIOE, 4, 1); 
		gpio_set(GPIOE, 5, 0); 
		delay_ms(60);
		gpio_set(GPIOE, 3, 1); 
		gpio_set(GPIOE, 4, 0); 
		delay_ms(60);
	}
	
	// below is legacy test programs for OPR1 
	
	while (1) { 								// test program: tilt throttle 
		// timing calculations:
		// at full 80 MHz HSI, APB1 runs at same 80 MHz 
		// PWM freq = APB1 / PSC / ARR 
		// 80 MHz / 80 [PSC] / 10000 [ARR] = 100 Hz
		
		GPIOD->MODER |= 2 << (15*2); 			// configure gpio afr to tim4 ch4 
		GPIOD->AFR[1] = 2 << (7*4); 
		
		RCC->APB1ENR1 |= 1<<2; 					// enable TIM4 
		
		TIM4->PSC = 80; 						// clock prescaler 
		TIM4->CCER = 1<<12;						// 
		TIM4->CCMR2 = (6 << 12) | (1 << 11);	// pwm mode, enable 
		TIM4->EGR = 1<<4; 						// give an event trigger to update shadow registers 
		TIM4->ARR = 10000;						// reload register 
		TIM4->CCR4 = 1000;					
		TIM4->CR1 = 
			(1 << 7) | 1; 						// enable auto reload preload and enable tim4 
		
		
		while (1) { // pre programmed program for rig testing on 2023 10 28 
			gpio_set(GPIOG, 9, 1); 
			TIM4->CCR4 = 1500; // rc protocol: 1 ms is minimum, 2 ms is maximum 
			nop(0x6FFFFFF); 
			gpio_set(GPIOG, 9, 0); 
			TIM4->CCR4 = 2000; // rc protocol: 1 ms is minimum, 2 ms is maximum 
			nop(0x6FFFFFF); 
			while (1) {
				for (int i = 0; i < 1000; i++) {
					TIM4->CCR4 = 1000 + i;
					nop(0xFFFF);
				}
			}
		}
		
		// while (1) { // tilt throttle loop 
		// 	int th = abs16(op1_imu_read_acel_x());
		// 	GPIOD->ODR = (GPIOD->ODR & 0xFFFFFF00) | (th>>8) & 0xFF;
		// 	int th_scale = th * 10000 / 0xFFFF * 4; // convert acel reading to gyro. multiply by full scale of acel sensor (4) 
		// 	TIM4->CCR4 = 1000 + th_scale / 10; // rc protocol: 1 ms is minimum, 2 ms is maximum 
		// 	nop(10000);
		// }
		
	}
	
	
	
	
	
	
	
	
	
	
}

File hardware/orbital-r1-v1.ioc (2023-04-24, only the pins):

Mcu.UserName=STM32L476ZGTx
PA0.Signal=ADCx_IN5
PA1.Signal=ADCx_IN6
PA10.Signal=USB_OTG_FS_ID
PA11.Signal=USB_OTG_FS_DM
PA12.Signal=USB_OTG_FS_DP
PA2.Signal=ADCx_IN7
PA3.Signal=ADCx_IN8
PA4.Signal=ADCx_IN9
PA5.Signal=ADCx_IN10
PA6.Signal=ADCx_IN11
PA7.Signal=ADCx_IN12
PA9.Signal=USART1_TX
PB0.Signal=QUADSPI_BK1_IO1
PB1.Signal=QUADSPI_BK1_IO0
PB10.GPIO_Label=GPIO_BTN0
PB10.Signal=GPIO_Input
PB11.GPIO_Label=GPIO_BTN1
PB11.Signal=GPIO_Input
PB12.Signal=SPI2_NSS
PB13.Signal=SPI2_SCK
PB14.Signal=SPI2_MISO
PB15.Signal=SPI2_MOSI
PB5.GPIO_Label=GPIO_MAG_DRDY
PB5.Signal=GPIO_Input
PB6.GPIO_Label=GPIO_RADPA_PWRCTL
PB6.Signal=GPIO_Output
PB7.GPIO_Label=GPIO_RADSW_CTL
PB7.Signal=GPIO_Output
PB8.GPIO_Label=GPIO_RADF_MUX
PB8.Signal=GPIO_Output
PB9.GPIO_Label=GPIO_RADF_MUXOUT
PB9.Signal=GPIO_Output
PC0.Signal=I2C3_SCL
PC1.Signal=I2C3_SDA
PC10.Signal=SPI3_SCK
PC11.Signal=SPI3_MISO
PC12.Signal=SPI3_MOSI
PC13.GPIO_Label=GPIO_VBUSOUT_EN
PC13.Signal=GPIO_Output
PC2.Signal=ADCx_IN3
PC3.Signal=ADCx_IN4
PC4.Signal=USART3_TX
PC5.Signal=USART3_RX
PD0.Signal=GPIO_Analog
PD1.Signal=GPIO_Analog
PD10.Signal=GPIO_Analog
PD11.Signal=GPIO_Analog
PD12.Signal=GPIO_Analog
PD13.Signal=GPIO_Analog
PD14.Signal=GPIO_Analog
PD15.Signal=GPIO_Analog
PD2.Signal=GPIO_Analog
PD3.Signal=GPIO_Analog
PD4.Signal=GPIO_Analog
PD5.Signal=GPIO_Analog
PD6.Signal=GPIO_Analog
PD7.Signal=GPIO_Analog
PD8.Signal=GPIO_Analog
PD9.Signal=GPIO_Analog
PE0.GPIO_Label=GPIO_RADF_TRCLK
PE0.Signal=GPIO_Output
PE1.GPIO_Label=GPIO_RADF_TRDATA
PE1.Signal=GPIO_Output
PE10.Signal=QUADSPI_CLK
PE11.Signal=QUADSPI_NCS
PE12.Signal=SPI1_NSS
PE13.Signal=SPI1_SCK
PE14.Signal=QUADSPI_BK1_IO2
PE15.Signal=QUADSPI_BK1_IO3
PE2.GPIO_Label=GPIO_LED_HEARTBEAT
PE2.Signal=GPIO_Output
PE3.GPIO_Label=GPIO_RADM_ONOFF
PE3.Signal=GPIO_Output
PF0.GPIO_Label=AVIBUS_I2C2_SDA
PF0.Signal=I2C2_SDA
PF1.GPIO_Label=AVIBUS_I2C2_SCL
PF1.Signal=I2C2_SCL
PF10.GPIO_Label=GPIO_STACK_IBUS_INT0
PF10.Signal=GPIO_Input
PF2.GPIO_Label=GPIO_RADF_SYNCWORD
PF2.Signal=GPIO_Input
PF3.GPIO_Label=GPIO_RADF_CE
PF3.Signal=GPIO_Output
PF7.GPIO_Label=GPIO_STACK_BUS_GOOD
PF7.Signal=GPIO_Input
PF8.GPIO_Label=ERRATA_GPIO_PA_EN
PF8.Signal=GPIO_Output
PF9.GPIO_Label=GPIO_STACK_RBUS_INT0
PF9.Signal=GPIO_Input
PG10.Signal=USART1_RX
PG11.GPIO_Label=GPIO_LEDA
PG11.Signal=GPIO_Output
PG12.GPIO_Label=GPIO_LEDB
PG12.Signal=GPIO_Output
PG13.Signal=I2C1_SDA
PG14.Signal=I2C1_SCL
PG3.Signal=SPI1_MISO
PG4.Signal=SPI1_MOSI
PG6.GPIO_Label=GPIO_LED_ALLGOOD
PG6.Signal=GPIO_Output
PG7.GPIO_Label=GPIO_LED_FAULT
PG7.Signal=GPIO_Output
PG9.GPIO_Label=GPIO_LEDC
PG9.Signal=GPIO_Output

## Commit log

2023-04-24 initial commit r1 hardware
    [orbital-r1.SchDoc, r1 bom 4 selected.xls, r1-xy.csv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]
2023-04-24 initial commit (seni working i2c)
2023-04-24 working on i2c
2023-04-24 i2c progress
2023-04-24 change to software i2c
2023-04-24 demo with mag temperature
2023-04-25 some imu
2023-04-25 imu functions and i2c probe
2023-04-26 silly magnetometer
2023-11-13 pinout doc and code for rig test
    [opr2 pinout.xlsx]
